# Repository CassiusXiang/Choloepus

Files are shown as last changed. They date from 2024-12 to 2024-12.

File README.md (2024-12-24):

# Choloepus



## Introduction
Choloepus is a flexible gripper driven by a three-phase motor with Field-Oriented Control (FOC).

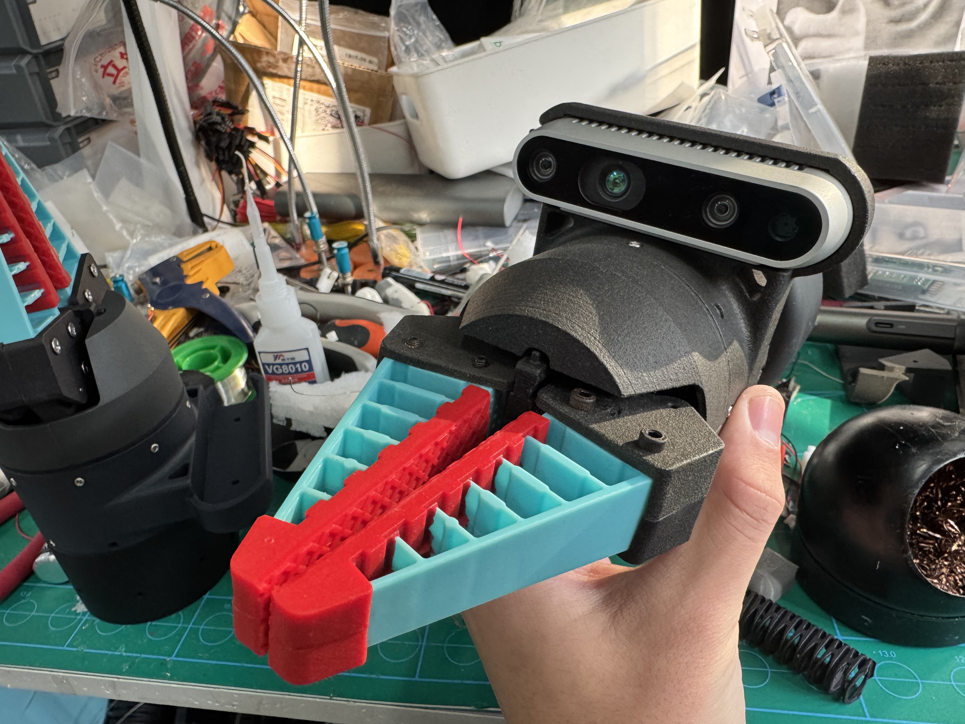
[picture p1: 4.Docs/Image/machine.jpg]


## Performance & Features

- Capable of lifting **3kg of water**
- Capable of delicate operations such as **picking up a needle** or **gripping an eggshell** ([video demo](https://youtu.be/MMdkBzw2Btk))
- Maximum drive current: **2A**
- Drive voltage range: **12V ~ 24V**
- Supports three control modes:
  - **Force closed-loop** (current loop)
  - **Position closed-loop**
  - **Hybrid force-position control**
- Weight: **300g**

## Mechanical Structure

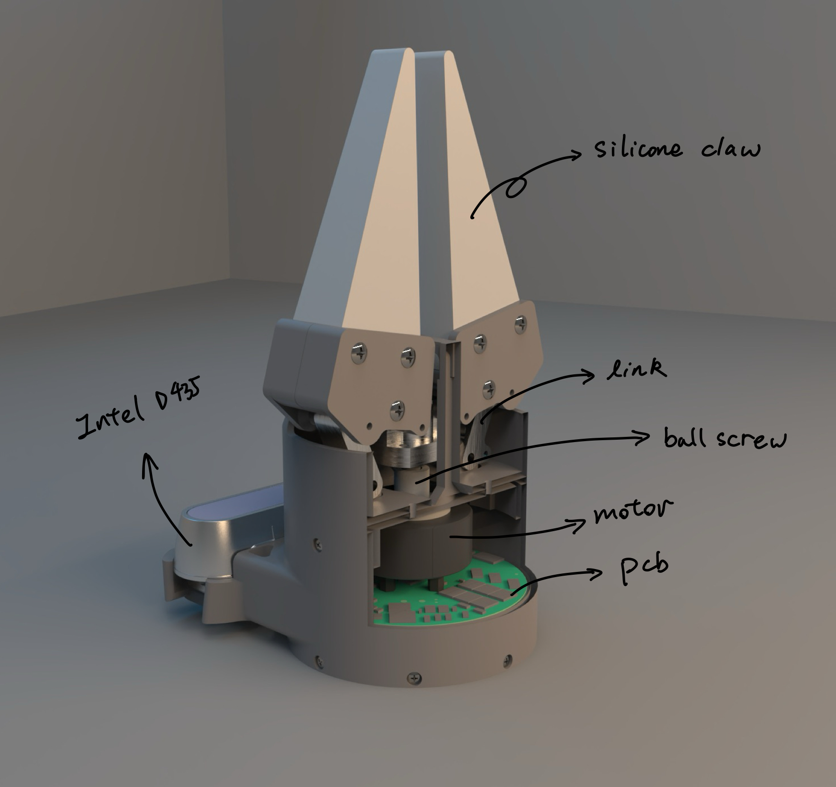
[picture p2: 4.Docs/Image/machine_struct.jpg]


Except for the motor and the depth camera, all other components were designed in-house. They can be fabricated via 3D printing and basic mechanical processing. You can find the models and engineering drawings in the `/0.Model` directory.

## Circuit Design

| Key Design | Details |
|---|---|
| Main MCU | ESP32-WROOM-32E |
| Communication | CAN, TTL |
| PCB Layers | 4 layers |
| Drive Method | H-bridge using 6 MOSFETs |
| Current Sensing | Comparator amplifier + shunt resistor  |
| Position Sensing| AS5600 Hall sensor |
| Drive Power | 24V -> 12V DC-DC buck |
| Control Power | 24V -> 5V DC-DC buck, 5V -> 3.3V LDO |

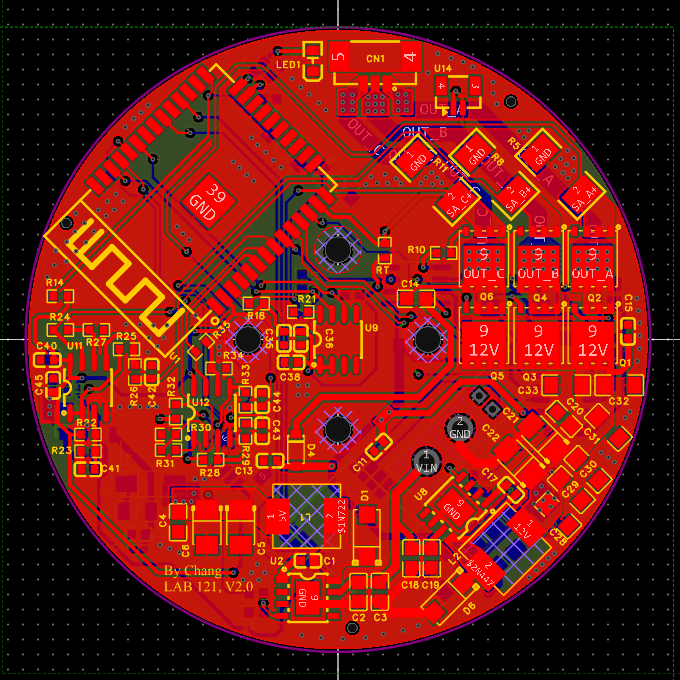
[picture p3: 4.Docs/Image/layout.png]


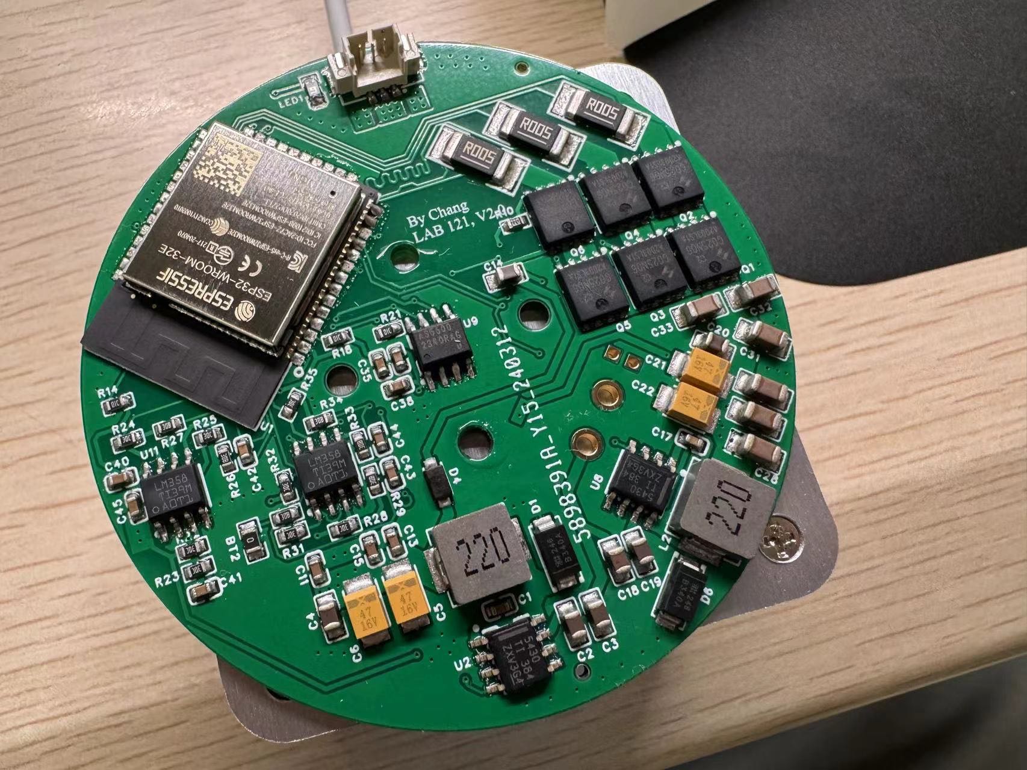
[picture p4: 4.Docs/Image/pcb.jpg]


You can find the circuit schematics and PCB layout in `./Hardware`.

## Firmware

This project’s firmware is developed with PlatformIO under the Arduino framework.

We have built upon the open-source project [SimpleFOC](https://github.com/simplefoc/Arduino-FOC-drivers) and made optimizations to drive the flexible gripper with FOC control.

The firmware is located in `./2.Frimware`.

## Communication

At the bottom of Choloepus, there is a 4-PIN XT30 connector that supports a DC input voltage of **12 ~ 24V** and **CAN bus** communication.

In the `/3.Software` directory, you will find a Python library that lets you create a Choloepus object and establish communication:
```python
my_gripper = gripper(serial_port='COM10', id_num=20)
```
Choloepus supports different control modes, shown below:
| **Control Mode** | **Command Frequency** | **Interruptible by New Commands** |
|---|---|---|
| **Position Control** | < 250Hz | Yes |
| **Force Control** | < 50Hz | Yes |
| **Hybrid Force-Position** | < 20Hz | Yes |

## Video Demo
[Watch the Demo](https://youtu.be/MMdkBzw2Btk)

This video demonstrates how Choloepus collaborates with a continuum robotic arm designed in our lab to perform a grape suturing operation.

## License
Choloepus is released under the AGPL-3.0. For more details, please refer to the LICENSE.

## Contact
Feel free to reach out to me at: changxiangchina@outlook.com

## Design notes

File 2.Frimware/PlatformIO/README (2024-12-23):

Choloepus_fw is the firmware for the flexible gripper, developed using PlatformIO on an ESP32.
Serial_tool_fw is a simple serial communication program used to write parameters to the CAN-TTL module from an external source.

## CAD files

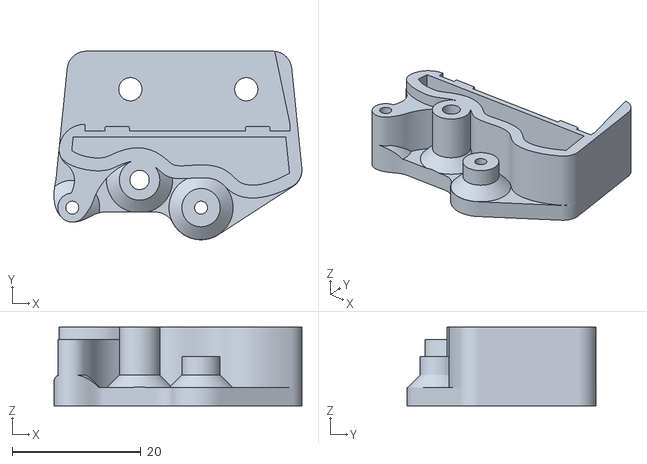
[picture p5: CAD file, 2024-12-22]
0.Model/STL/Flexible_Claw_Connection (Mirror).STL
38.5 x 29.3 x 12.2

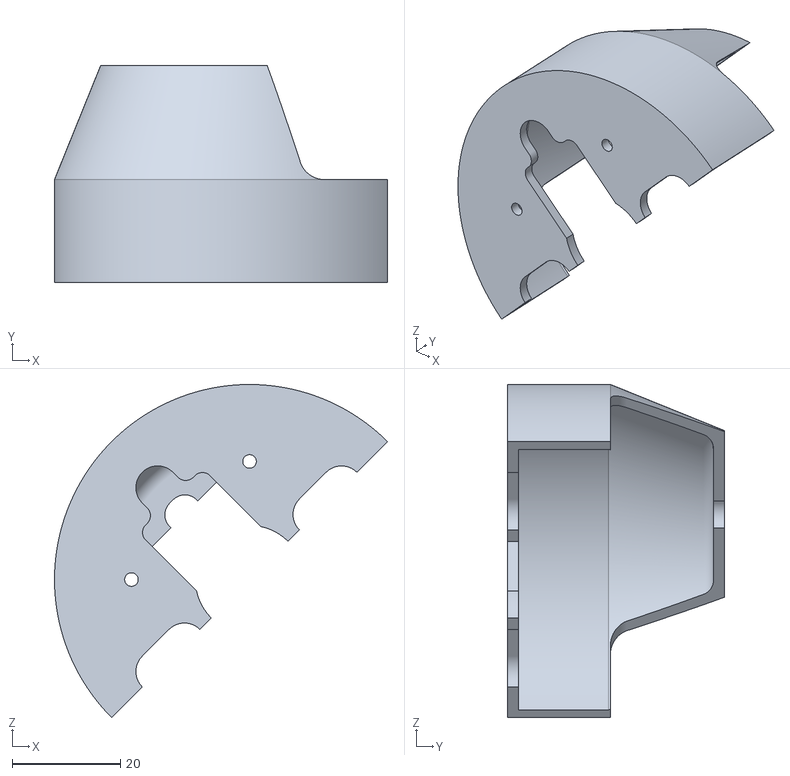
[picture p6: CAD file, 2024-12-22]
0.Model/STL/Half_Protective_Shell.STL
61.5 x 40.0 x 61.5

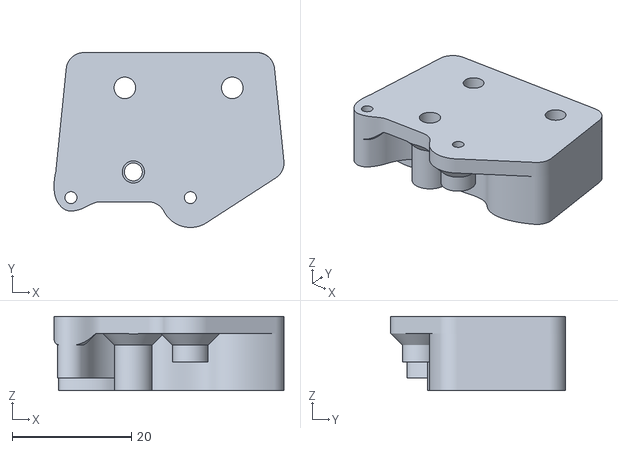
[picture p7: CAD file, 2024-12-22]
0.Model/STL/Flexible_Claw_Connection.STL
38.5 x 29.3 x 12.4

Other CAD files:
0.Model/DWG/SFK0601Ball-Screw.DWG

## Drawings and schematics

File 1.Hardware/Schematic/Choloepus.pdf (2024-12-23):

## 3V3R¹⁸ 10k

## RSTC³⁷ 100nF

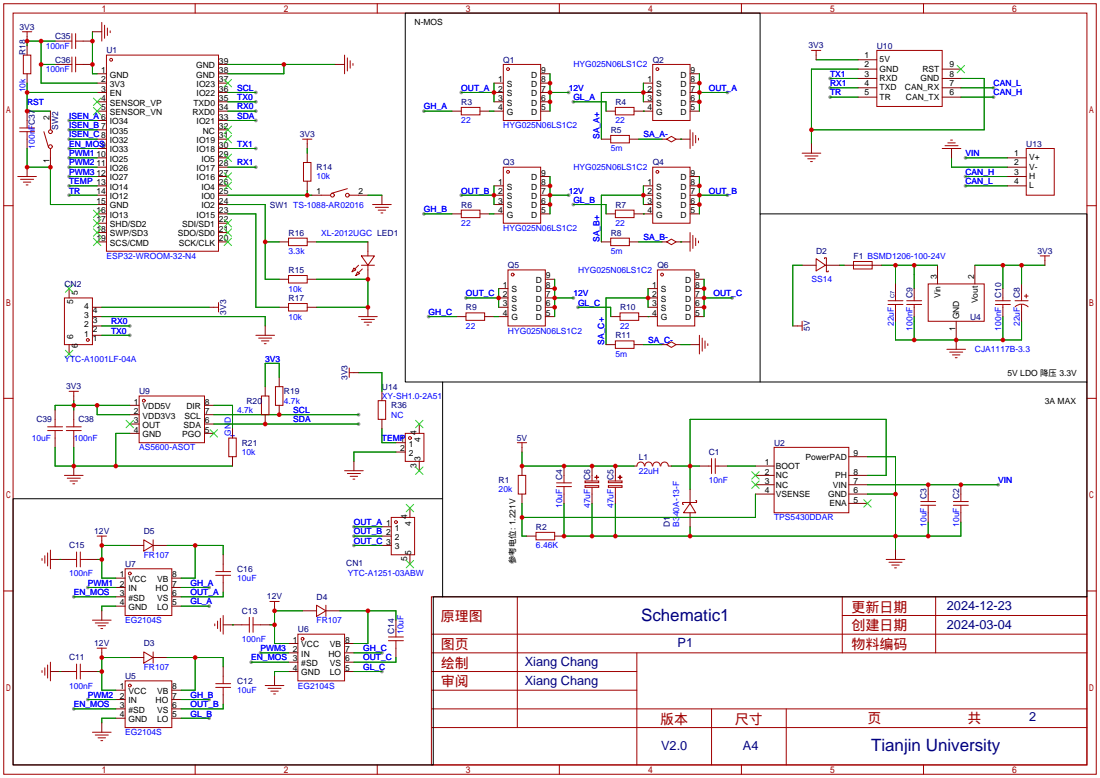
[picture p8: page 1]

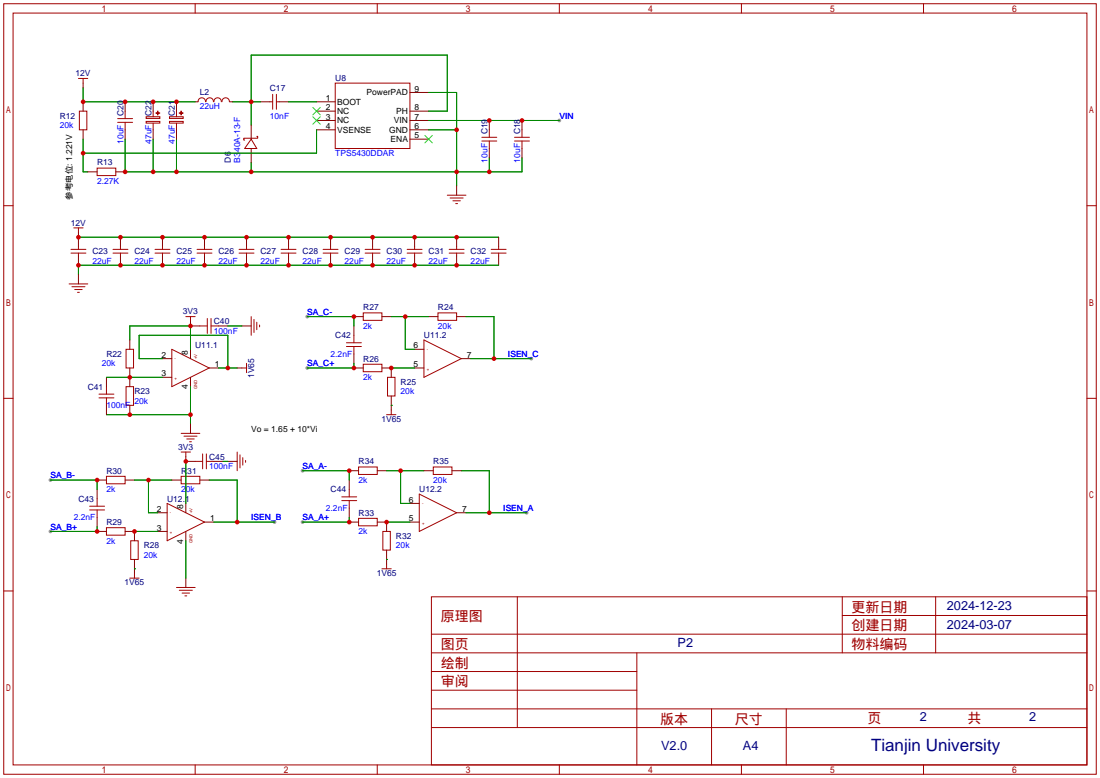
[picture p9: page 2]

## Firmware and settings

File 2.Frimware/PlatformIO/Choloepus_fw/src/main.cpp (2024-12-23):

/**
 * For Flexible_jaws controller
 * by X.Chang@Version1.0
 * LAB_121
 * 参数笔记
 * 最大张角对应传感器机械角度 0rad
 * 最小张角对应传感器机械角度 90rad
 * @version: v2.1.2
 */

#include <SimpleFOC.h>
#include <iostream>
#include <vector>
#include <stdexcept>
#include <cstdint>
#include <cstring>
// #include <WiFi.h>

// 任务句柄
TaskHandle_t Task1;
TaskHandle_t Task2;
// I2C 磁编码器实例初始化
MagneticSensorI2C sensor = MagneticSensorI2C(AS5600_I2C);

// 电机实例初始化
BLDCMotor motor = BLDCMotor(7);                         // 初始化一个motor实例，极对数为7
BLDCDriver3PWM driver = BLDCDriver3PWM(25, 26, 27, 33); // 绑定三相电机驱动的 PWM 引脚

// 引脚定义
// const int TX1 = 18;
// const int RX1 = 17;

// dirction
const int left_hand = 1;

// 角度设置变量
float target = 0; // 目标

// 命令解释器的初始化
Commander command = Commander(Serial);
void doTarget(char *cmd) { command.scalar(&target, cmd); }
void onMotor(char *cmd) { command.motor(&motor, cmd); }
// 自定义函数
int32_t decodeToTwosComplement(const std::vector<uint8_t> &byteList) // decode
{
    if (byteList.size() < 4)
    {
        std::cerr << "Error: Byte list must contain at least 4 bytes." << std::endl;
        return 0;
    }

    // 将字节序列直接解释为一个32位有符号整数
    int32_t number;
    memcpy(&number, byteList.data(), sizeof(number));

    return number;
}

std::vector<uint8_t> getSubVector(const std::vector<uint8_t> &originalVector, int start, int end)
{ // 用来分割vector
    // 请注意，end 是不包含在内的，所以实际上是到 end - 1 的元素
    return std::vector<uint8_t>(originalVector.begin() + start, originalVector.begin() + end);
}

std::vector<int32_t> getModeSpeed(const std::vector<uint8_t> &originalVector)
{
    std::vector<int32_t> res = {};
    std::vector<uint8_t> originalVector1 = getSubVector(originalVector, 8, 12);
    std::vector<uint8_t> originalVector2 = getSubVector(originalVector, 12, 16);
    int32_t mode = decodeToTwosComplement(originalVector1);
    int32_t speed = decodeToTwosComplement(originalVector2);
    res.push_back(mode);
    res.push_back(speed);

    return res;
}

bool checkId(const std::vector<uint8_t> &originalVector)
{
    if (originalVector[7] == 0x14)
    {
        return true;
    }
    else
        return false;
}

// 定义任务函数
void Task1code(void *pvParameters)
{ // FOC control
    // 引脚初始化

    for (;;)
    {
        // main FOC algorithm function
        // the faster you run this function the better
        // Arduino UNO loop  ~1kHz
        // Bluepill loop ~10kHz
        motor.loopFOC();

        // Motion control function
        // velocity, position or voltage (defined in motor.controller)
        // this function can be run at much lower frequency than loopFOC() function
        // You can also use motor.move() and set the motor.target in the code
        motor.move(left_hand * target);

        // function intended to be used with serial plotter to monitor motor variables
        // significantly slowing the execution down!!!!
        // motor.monitor();
        // if (motor.)

        // user communication
        // command.run();

        // vTaskDelay(1 / portTICK_PERIOD_MS);
    }
}

void Task2code(void *pvParameters)
{
    vTaskDelay(1000 / portTICK_PERIOD_MS); // 等待主控制程序启动
    Serial.println("setting...");
    motor.controller = MotionControlType::torque;
    target = 1.4;
    vTaskDelay(5000 / portTICK_PERIOD_MS); // 初始化
    target = 0;
    motor.sensor_offset = -sensor.getAngle();
    Serial.println("setting success");

    int serp = 0;

    for (;;) // 命令解码器
    {
        if (Serial1.available() > 0)
        {
            std::vector<uint8_t> data;
            int mode, value;
            while (Serial1.available() > 0)
            {
                data.push_back(Serial1.read());
            }
            // Serial.write(Serial1.read());s
            // Serial.write(data[0]);
            // Serial.write(data[1]);
            // Serial.write(data[2]);
            // Serial.write(data[3]);
            // Serial.write(data[4]);
            // Serial.write(data[5]);
            // Serial.write(data[6]);
            // Serial.write(data[7]);
            // Serial.write(data[8]);
            // Serial.write(data[9]);
            // Serial.write(data[10]);
            // Serial.write(data[11]);
            // Serial.write(data[12]);
            // Serial.write(data[13]);
            // Serial.write(data[14]);
            // Serial.write(data[15]);
            // Serial.println(data.size());
            if (data.size() == 16 && checkId(data))
            {
                mode = data[8];
                value = (data[9] << 8) + data[10];
                // --- debug ---
                // Serial.print(mode);
                // Serial.print(" ");
                // Serial.print(value);
                // Serial.println();
                // --- ----- ---
                switch (mode)
                {
                case 0:
                    motor.controller = MotionControlType::torque;
                    target = 1.4;
                    vTaskDelay(5000 / portTICK_PERIOD_MS); // 初始化
                    target = 0, motor.sensor_offset = sensor.getAngle();
                    break;

                case 1:
                    motor.controller = MotionControlType::torque; // 力矩控制
                    target = value / 100.0;
                    break;

                case 2:
                    motor.controller = MotionControlType::angle; // 角度控制
                    target = 0 - value / 100.0;
                    break;
                }
                data.clear();
            }
        }
        // serp ++;
        // if(serp == 100){
        //     Serial.println();
        // }
        // Protect
        // if (sensor.getAngle() < 0)
        // {
        //     motor.controller = MotionControlType::torque;
        //     target = 0;
        //     Serial.println("angle overrun");
        // }

        vTaskDelay(3 / portTICK_PERIOD_MS);
    }
}

void setup()
{

    // 传感器
    sensor.init();             // 初始化磁传感器
    motor.linkSensor(&sensor); // 将电机与传感器连接

    // 电机驱动配置
    driver.voltage_power_supply = 12; // 供电电压
    driver.init();                    // 驱动初始化
    motor.linkDriver(&driver);        // 绑定驱动与电机

    // FOC控制模式选择
    motor.foc_modulation = FOCModulationType::SpaceVectorPWM;

    // 运动控制环的配置
    // motor.controller = MotionControlType::velocity; // 速度环
    motor.controller = MotionControlType::torque; // 力矩环

    // 控制部分的配置
    // default parameters in defaults.h

    // velocity PI control
    motor.PID_velocity.P = 0.2;
    motor.PID_velocity.I = 2;
    // max velocity
    motor.voltage_limit = 6;
    motor.voltage_sensor_align = 1;

    // velocity low pass filtering time constant
    // the lower the less filtered
    motor.LPF_velocity.Tf = 0.05;

    // angle P controller
    motor.P_angle.P = 20;
    // maximal velocity of the position control
    motor.velocity_limit = 12;

    motor.sensor_offset = 1.78;              // Set the zero electrical angle
    motor.sensor_direction = Direction::CCW; // Set the sensor direction to counter-clockwise

    // use monitoring with serial
    Serial.begin(115200);
    // Serial1.begin(115200);
    Serial1.begin(115200, SERIAL_8N1, 18, 17);
    // comment out if not needed
    motor.useMonitoring(Serial);

    // initialize motor
    motor.init();
    // align sensor and start FOC
    // motor.();
    motor.initFOC();
    // motor.initFOC(4.56, Direction::CW);
    // motor.initFOC(2.25, Direction::CCW);
    // 需要增加跳过矫正 参考http://simplefoc.cn/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

    // add target command T
    // command.add('T', doTarget, "target angle");
    // command.add('M', onMotor, "my motor");

    Serial.println(F("Motor ready"));

    _delay(1000);

    // 创建任务
    xTaskCreatePinnedToCore(
        Task1code, /* 任务函数 */
        "Task1",   /* 任务名字 */
        50000,     /* 栈大小 */
        NULL,      /* 传递给任务函数的参数 */
        1,         /* 优先级 */
        &Task1,    /* 任务句柄 */
        0);        /* 核心编号 */
    xTaskCreatePinnedToCore(
        Task2code,
        "Task2",
        50000,
        NULL,
        1,
        &Task2,
        1);
}

void loop()
{
    // nothing
}

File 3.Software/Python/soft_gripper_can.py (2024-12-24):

# -*- coding=utf-8 -*-

""" soft_gripper 二指FOC柔性夹爪Python函数库(面向对象)

@ Version
v2.1.2(basic-hardware-software)

@ public function brief

@ can 参数
1. mode : 包模式
2. baudrate : 100,000bps(1Mbps)

@author
Xiang Chang Tianjin University

@email
changxiangchina@outlook.com

"""


class gripper:
    def __init__(self, serial_port, ID):
        self.serial_port = serial_port  # 已经打开的串口对象
        self.ID = ID
        
    # Public ---------------------------------------------------------------
        
    def set_angle(self, angle):
        data = format_data(angle, 0x02, self.ID)
        self.send_command(data=data)
        
    def reset_angle(self):
        data = format_data(0x00, 0x00, self.ID)
        self.send_command(data=data)
        
    def set_torque(self, torque):
        data = format_data(torque, 0x01, self.ID)
        self.send_command(data=data)
        
    # 类私有函数 ------------------------------------------------------------
    # CAN发送函数
    def send_command(self, cmd=0x09, data=[], rtr=0):
        cdata = [0x08, 0, 0, 0x00, 0x00, 0x00, 0x00, 0x00, 0x00, 0x00, 0x00]
        id_list = (self.ID << 5) + cmd # id号右移5位 + cmd，此处根据odrive CAN node_id号与cmd_id的角度关系决定
        cdata[1] = id_list >> 8
        cdata[2] = id_list & 0xFF
        for i in range(8):
            cdata[3 + i] = data[i] # data[]中包含命令的内容，如角度、转速、转矩等
        # print("cdata: ", cdata)
        data = can_to_uart(data=cdata, rtr=rtr)
        # print("send_command: ", data)
        self.write_data(data)
        # write_data(data=can_to_uart(data=cdata, rtr=rtr))
        
        # NOTE: the recive data of esp32 is cdata

    # 串口发送函数
    def write_data(self, data=[]):
        try:
            result = self.serial_port.write(data)  # 写数据
            # print("write_data: ", data)
            return result
        except Exception as e:
            print("---error in write_data--:", e)
            print("restart the serial...")
            self.serial_port.close()
            self.serial_port.open()
            result = self.serial_port.write(data)  # 写数据
            return result

# USB转CAN模块包模式：CAN报文->串行帧
def can_to_uart(data=[], rtr=0):
    udata = [0xAA, 0, 0, 0x08, 0, 0, 0, 0, 0x00, 0x00, 0x00, 0x00, 0x00, 0x00, 0x00, 0x00] # 其中0x08代表CAN读取字头中的DLC（报文长度）
    # udata[1]对应CAN字头中的IDE，udata[2]对应CAN字头中的RTR，udata[3]对应CAN字头中的DLC，udata[4~7]对应id
    # udata 根据USB转CAN模块串口包模式定义
    if len(data) == 11 and data[0] == 0x08: # 0x08 为预设的一个校验字节
        if rtr == 1:
            udata[2] = 0x01 # rtr 标志位
        for i in range(10):
            udata[6 + i] = data[i + 1]
        return udata
    else:
        return []

# 格式化数据
# value : 浮点型数据

def format_data(value, mode, id):
    # value 16bit
    # mode 8bit
    # id 16bit
    rdata = [0x00, 0x00, 0x00, 0x00, 0x00, 0x00, 0x00, 0x00]
    value = range_constrian(value, 1, 90)
    value = round(value, 2) * 100
    rdata[0] = id >> 8
    rdata[1] = id & 0xFF
    rdata[2] = mode
    # mode = 0 : 力矩控制
    # mode = 1 : 位置控制
    rdata[3] = int(value) >> 8 # high
    rdata[4] = int(value) & 0xFF # low
    # print(rdata)
    return rdata

def range_constrian(value, low, high):
    if value <= low:
        return low
    elif value >= high:
        return high
    return value

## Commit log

2024-12-22 [Model] Add .STL and DWG
    [Flexible_Claw_Connection (Mirror).STL, Flexible_Claw_Connection.STL, Half_Protective_Shell.STL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]
2024-12-23 [Frimware] add ESP32 fw
2024-12-23 [Hardware] add pcb and sch
    [1_P2.schdoc.schdoc, 2_P1.schdoc.schdoc, PCB1.pcbdoc]
